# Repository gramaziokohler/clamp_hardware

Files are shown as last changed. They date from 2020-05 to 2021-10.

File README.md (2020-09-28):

# clamp_hardware

Mechanical design for remote controlled robotic actuators. This includes various clamps and grippers. 

This repo is part of the [Robotic Assembled Timber Structures with Integral Timber Joints](https://github.com/gramaziokohler/phd_spatial_timber_assembly) project. 

## Repo folder structure

Mechanical design files (Rhino 3D files, production drawings), ordered by clamp and gripper types:

- **/clamps** - Robotic clamp design 
- **/grippers** - Robotic gripper design

Experiment setup (Rhino 3D files, photographs, writeup) including results and interpretation.

- **/experiments** - Physical tests constructed and performed to validate mechanical design.

## Design Goals

The mechanical design of the clamps is to be able to achieve the following functions: 

- Deliver high assembly force to assemble tight-fitting timber joints
- The clamps cannot relocate itself but rely on robotic manipulator (such as a robotic arm) for locomotion.
- The clamps can be temporarily attached to a timber beam and operate remotely.
- Different clamp designs accommodate different types of timber joints, some clamp design can accommodate a joint type with various angles.

## Clamp Design

### Clamp CL1

**Cross Lap Joint** Clamp for **Planar Orthogonal** joint angle. Timber section size 100mm x 100mm.

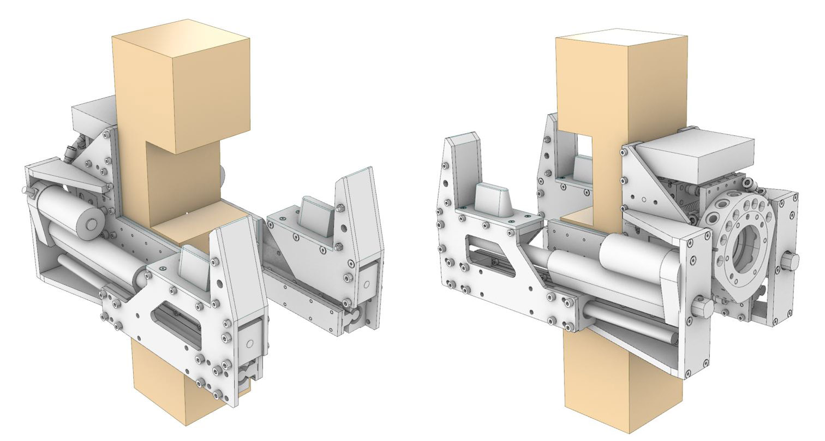
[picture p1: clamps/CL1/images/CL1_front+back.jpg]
CL1_front+back


This is the first clamp prototype with off-the-shelf actuator and two jaw design. This proof-of-concept device successfully performed a single joint assembly task. 

This prototype exposed the limitation of off-the-self linear actuators which were designed to deliver push force, not pull force. 

- Maximum assembly force ~400kgf.
- Robotic quick changer integrated but not tested
- No remote control capability
- Linear actuator gear box housing failed during stress test

### Clamp CL2

**Cross Lap Joint** Clamp for **Planar Orthogonal** joint angle. (similar to CL1)

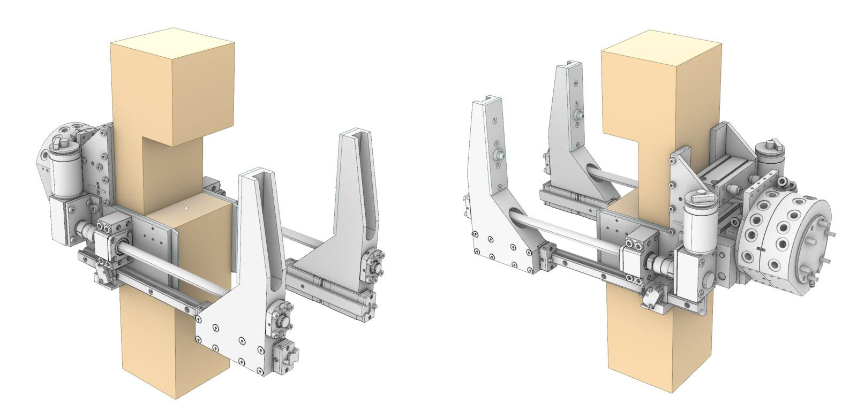
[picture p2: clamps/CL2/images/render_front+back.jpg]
render_front+back


This clamp is an improved version from **CL1** with similar design goals and capability. The main modification is the development of a **single piece jaw design** by combining linear guide mount and ball nut mount into a single piece of milled aluminum. This jaw design is the result of two important experiments mentioned in the next section.

Notable improvements:

- Reliable power transfer mechanism
- Reliable DC Encoder motor
- Lighter weight than CL1
- Modular jaw construction

This clamp was designed and materials were prepared but were never assembled for testing. The materials was then used to create TL1 for the Tokyo project. Since the tests performed with TL1 was successful and the 

### Clamp TL1 (tokyo)

**Tee Lap Joint** Clamp for **Planar Variable** joint angle. Timber section size 120mm x 120mm.

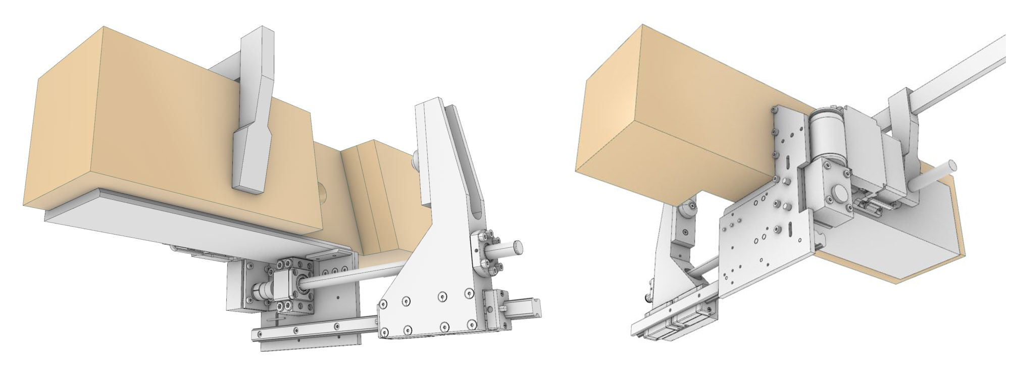
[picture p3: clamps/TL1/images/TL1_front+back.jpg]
TL1_front+back


This clamp is designed specifically for the GKR Tokyo Pavilion project with revised linear actuator design using ball screw and encoder DC motor. It has one clamp jaw that presses on the middle of the lap joint.

Two units of this clamp was created and two experiments were performed on assembling timber beams in during the Tokyo project. 

- No robotic quick changer integration
- Remote control and battery operation tested
- Two way synchronization not tested

Notable mechanical features:

- Single piece jaw design (combining linear guide mount and ball nut mount)
- Highly reliable worm-geared DC motor with dual channel encoder
- Small number of custom-piece

### Clamp CL3

**Cross Lap Joint** Clamp for **Planar Variable** joint angle.

 render_front+back

CL3_Front+Back

This clamp is a continuation of the single piece jaw design originated from CL2 and tested in TL1. 

The clamp is used in the construction of Fred's Pavilion where the robotic quick changer is not integrated.

Battery Compartment Size: 82(L) x 37(W) x 46(H)

## Validation Experiments

[**Ball Screw Actuation Experiment**](./experiments/190910_Screw_And_Motor_Test) - After the failure of the prototype clamp CL1 with integrated linear actuator, the decision is to construct the linear actuation from ball screw and motor from parts. This test validate the selection of ball screw and motor by testing the pull force developed.

[**Linear Guide and Clamp Jaw Experiment**](./experiments/191111_Linear_Guide_Jaw_Test) - Learning from the experience of the prototype clamp CL1, the circular linear guide combination with linear actuator was insufficient to prevent small rotational movements. This experiment was devised to assess replacement with a rolling-ball linear guide and the corresponding clamp jaw design. The conclusion of this experiment leads to the development of the single-piece jaw design for clamp TL1 and CL2

[**Joint Press**](./experiments/200100_Joint_Press) - CNC controlled joint pressing machine to measure the tightness of a lap joint. (Device designed but not constructed)

[**Lap Joint Tightness vs Rotational Stiffness Experiment**](./experiments/191113_Joint_Tightness_Stiffness_Study) - Experiment to study the rotational stiffness of lap joints in relation to the tightness of the joint. Tightness is measured by the amount of assembly force used to assemble the joint. (Experiment planned but not performed due to budget constraint)

[**Hollow Screw Tightening Torque Measurement**](./experiments/200903_LucaScrewMeasurement)  - Experiment to study the tightening torque of Luca's hollow screw in wood. This allows gearbox and motor sizing for Clamp SL1 

Credits
-------------

This repository was created by Pok Yin Victor Leung <leung@arch.ethz.ch> [@yck011522 ](https://github.com/yck011522) at [@gramaziokohler](https://github.com/gramaziokohler)

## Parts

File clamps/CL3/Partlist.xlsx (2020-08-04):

Block Name | Total | 4 Clamps Total | Source
Arduino Nano (LoRes) | 1 | 4
CL3 Electronics Pack | 1 | 4
ControllerPCB | 1 | 4
Fixed End Support BK10 | 1 | 4
Flat Head Socket Screw M4x12 | 3 | 12 | PHY-Shop
Flat Head Socket Screw M4x16 | 4 | 16 | PHY-Shop
Flat Head Socket Screw M4x20 | 9 | 36 | PHY-Shop
Flat Head Socket Screw M4x30 | 2 | 8 | PHY-Shop | x
Flat Head Socket Screw M4x8 | 4 | 16 | PHY-Shop | x
Flat Head Socket Screw M5x10 | 2 | 8 | PHY-Shop | x
Flat Head Socket Screw M8x20 | 4 | 16 | RFL
GripperPin | 6 | 24
Hex Nut M5 | 6 | 24 | void
HGL15CA | 2 | 8
KJL06-01S | 2 | 8
KQ2V06-M5A1 | 2 | 8
KQ2V06-M5A1.step | 2 | 8
KQ2V06-M5A1.step_BUTTON_06O | 2 | 8
KQ2V06-M5A1.step_KQ2(V-VS-VD-VT-VF-Z-ZD-ZT-ZF)_V06-M5 | 2 | 8
KQ2V06-M5A1.step_STUD_VZC_M5 | 2 | 8
LED 5mm | 2 | 8
M10 SFU Nut | 1 | 4
Motor Driver XY160D | 1 | 4
MXQ16-40P.step_AxialPipingUnit_16 | 1 | 4
MXQ16-40P.step_MXQ3149Tube_16-40 | 1 | 4
MXQ16-40P.step_MXQTables_16-40 | 1 | 4
Omron V-155-1C25_MircoSwitch | 1 | 4
Phoenix Plug Female ScrewTerm 2Pos | 8 | 32
Phoenix Plug Female ScrewTerm 3Pos | 1 | 4
Phoenix Plug Male PCB 2Pos | 8 | 32
Phoenix Plug Male PCB 3Pos | 1 | 4
Rigid Coupler SRJ-25C-8 | 1 | 4
SFU 1204 Nut | 1 | 4
Socket Head Cap Screw M3x16 | 2 | 8 | PHY-Shop |  | x
Socket Head Cap Screw M3x20 | 2 | 8 | PHY-Shop |  | x
Socket Head Cap Screw M3x8 | 8 | 32 | PHY-Shop
Socket Head Cap Screw M4x12 | 9 | 36 | PHY-Shop |  | x
Socket Head Cap Screw M4x16 | 15 | 60 | PHY-Shop | Polish | x
Socket Head Cap Screw M4x50 | 1 | 4 | PHY-Shop |  | x
Socket Head Cap Screw M4x8 | 4 | 16 | PHY-Shop
Socket Head Cap Screw M5x20 | 1 | 4 | PHY-Shop |  | x
Socket Head Cap Screw M5x30 | 3 | 12 | PHY-Shop |  | x
Socket Head Cap Screw M6x16 | 1 | 4 | RFL
Socket Head Cap Screw M6x20 | 1 | 4 | RFL
Socket Head Cap Screw M6x35 | 6 | 24 | PHY-Shop |  | x
Wireless CC1101 | 1 | 4
Dowel Pin 8x16 or 8x15 | 1 | 4 | PHY-Shop |  | x
Dowel Pin 6x10 or 6x12 | 1 | 4 | PHY-Shop |  | x
Dowel Pin 5x10 5x12 | 2 | 8 | PHY-Shop |  | x

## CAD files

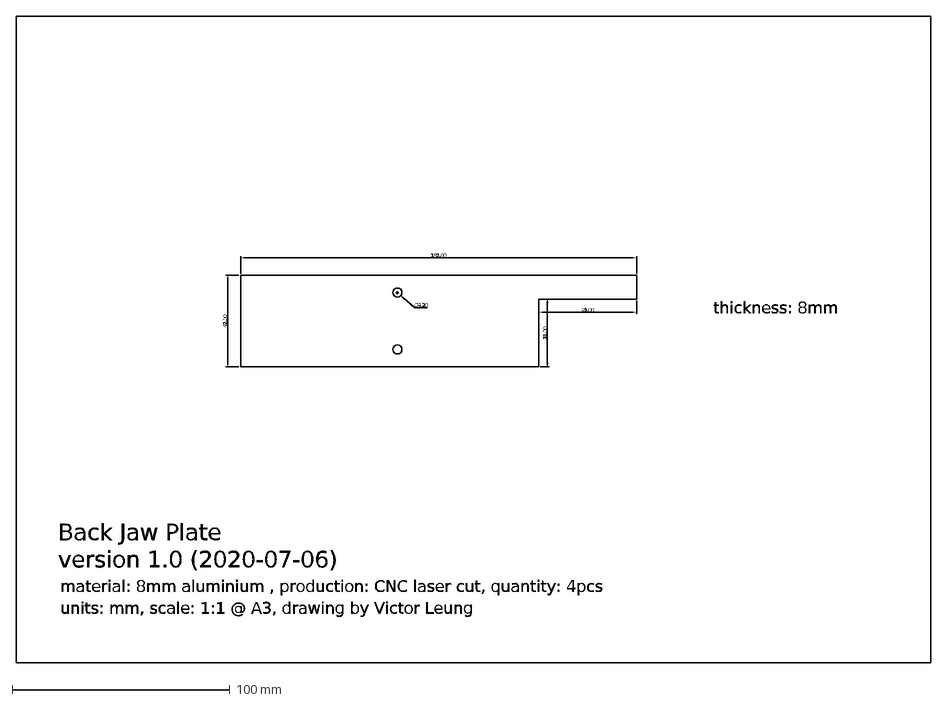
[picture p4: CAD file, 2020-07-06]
clamps/CL3/drawings/back_jaw_plate_v1.0.dxf
Ø4.20
31.00
45.00
42.00
182.00
material: 8mm aluminium , production: CNC laser cut, quantity: 4pcs
thickness: 8mm
Back Jaw Plate version 1.0 (2020-07-06)
units: mm, scale: 1:1 @ A3, drawing by Victor Leung

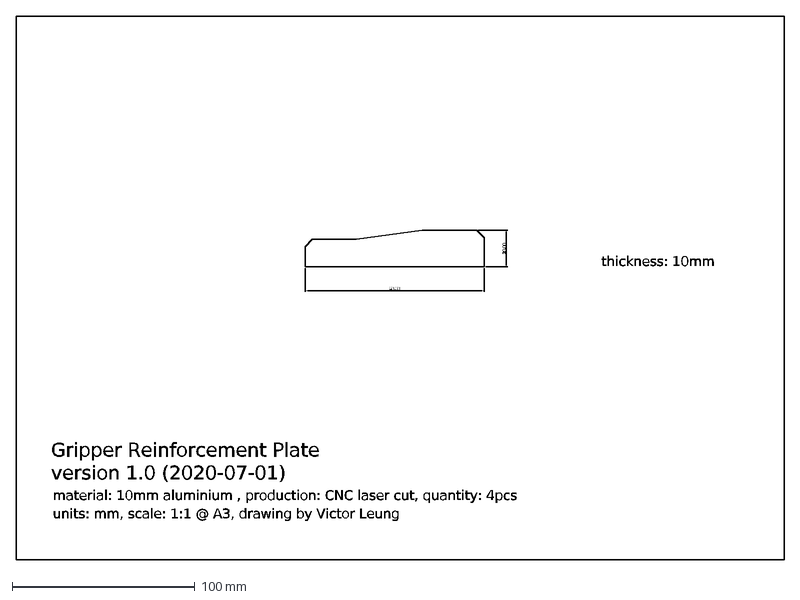
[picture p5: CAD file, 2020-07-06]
clamps/CL3/drawings/gripper_reinforcement_plate_v1.0.dxf
20.00
98.00
Gripper Reinforcement Plate version 1.0 (2020-07-01)
material: 10mm aluminium , production: CNC laser cut, quantity: 4pcs
thickness: 10mm
units: mm, scale: 1:1 @ A3, drawing by Victor Leung

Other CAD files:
drill_guide/3dp/drill_check_mainslide.3mf
clamps/SL1/3dp/MainBody.stl
camera/3dp/100mm_cover.stl
clamps/CL3/3dp/limit_switch_block.stl
clamps/SL1/3dp/SwitchHolder.3mf
drill_guide/3dp/32mm Drill guide.3mf
experiments/200109_Pickup_Station_Test/PickupStationAlignmentPeg3mm.stl
experiments/200115_Gripper_Nipple_Test/Jaw_NippleCone01.stl
experiments/200711_Robotic_PickPlace_Actions/3dp/clamp_jaw_pad_tester.stl
experiments/211023_ChamferPlaneAttachment/attachment_v1.3mf
grippers/PG/3dp/PGStorageBlock_i3mk2s.3mf
toolchanger/3dp/ts_dummy_base.stl
toolchanger/toolchanger_guide/3dp/robot_side_guide.stl
camera/3dp/100mm_stand.stl
clamps/CL3/3dp/jaw_pad.3mf
clamps/SL1/3dp/DriverCover.3mf
camera/3dp/70mm_cover.stl
camera/3dp/70mm_stand.stl
camera/3dp/MountPlate.stl
camera/3dp/MountStand.stl
camera/3dp/MountStand2.stl
camera/Aruco_marker_board.3dm
clamps/CL1/CL1_design.3dm
clamps/CL2/CL2_design.3dm
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

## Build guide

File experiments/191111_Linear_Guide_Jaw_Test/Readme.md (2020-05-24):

# Clamp Jaw Test

This set of test investigate the limiting criteria in jaw design. Especially in answering the following questions:

- Will the Linear Guide be overloaded?

- Can the linear guide be mounted cantilevered?

What is the minimum throat size of the L Shaped Jaw

What is the most flexible component in the system.

Motor 555 Gear 55:1

Test Date 2019-11-27 (till 28)

## Test 1 - Voltage vs Pull Force Test

The first test is to establish the relationship between voltage and pull force.

Similar to previous screw pull force test.

### Parameters

Different limiting current is used in each set, voltage is varied.

### Result

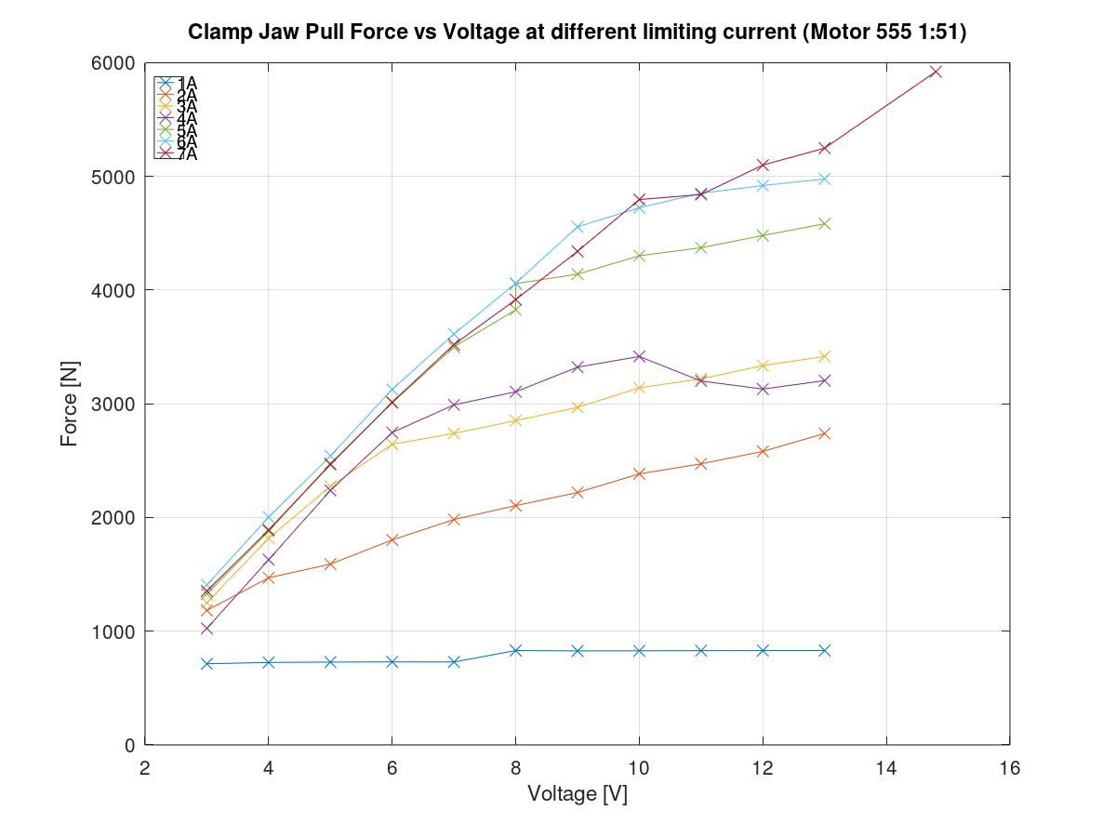
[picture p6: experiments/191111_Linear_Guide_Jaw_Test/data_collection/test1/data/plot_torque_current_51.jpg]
plot_torque_current_51


Note that the last data point of the 7A series at 14.4V is actually using the LiPo Battery as power source.

Two slopes can be seen here in the graph:

**The first steep slope** is when the motor is limited by the supplied voltage (Power supply in Constant voltage mode). Increase in supplied voltage is followed by an increase in supplied current. Therefore the motor can pull harder.

**The second slope** occurs at at point where the motor is limited by the set current limit. (Power supply is in constant current mode) The terminal current is limited and the motor will not be able to pull harder. However, there is still an increase in the pull force with voltage probably due to the higher voltage, hence faster motor speed and momentum, before terminal position. This momentum contribute to the final pulling force. 

## Test 2 - Spacing between linear bearing

Investigate different linear bearing spacing.

Look for difference in pull force, visual observation of L shape jaw deflection?

### Parameters

Test will involve 5 possible positions: 74mm, 87mm, 100mm, 126mm, 152mm.

Each position will use three different current: 3A, 4A, 5A

Voltage set beyond the current limit point of the 5A situation: 9V

### Result

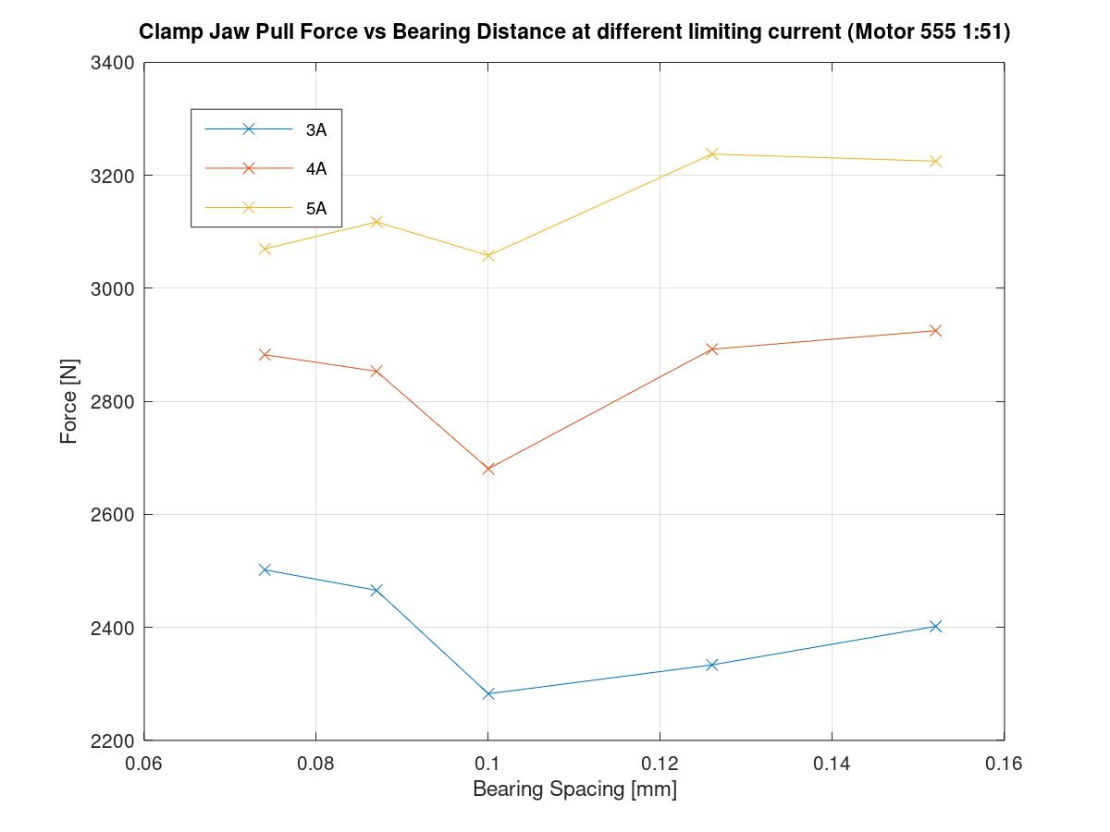
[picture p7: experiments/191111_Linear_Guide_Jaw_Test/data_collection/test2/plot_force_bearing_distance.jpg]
plot_force_bearing_distance


Only one set of data is collected. Due to time consumption in relocating the bearing.

However, it is still conclusive that the bearing distance do not have much effect on the pull force. 

We can conclude that the bearing distance in the clamp design, is only limited by overloading.

The bearing distance can be further reduced to 66mm in final design.

## Test 3 - Two bolts mounting Linear Rail

Investigate when the linear rail is more cantilevered. When only the last two bolts are used to hold it.

### Parameters

Fixed Voltage at 14V, current increase from 3A upwards.

The steel U profile is modified. The previous hole for the screw to go through is too small, the screw scratches on the steel.

| Current | Pull Force (Max Value) |
| --- | --- |
| 3 | 3154 |
| 4 | 4459 |
| 5 | 5167 |
| 6 | 5138 |
| 7 | 6086 |

Only one set of pull test is performed. As the jaw successfully puled about 6kN, the test was not continued to avoid damaging components.

### Result

- The structure deformed but remain intact after repeated pull test. 
- The linear rail do not deform at all, the steel is very strong.
- The Linear bearings even though at only 74mm spacing, do not seem to be overloaded.
- The L Shape Jawdeform the most. Perhaps if the L piece have a triangulated chamfer, the jaw structure could be more stiff. However, the plat interfere with the screw bearing.

## Test 4 - Worm drive gearbox

Investigate if the 555 motor paired with the GW4058 1:54 or 1:72 gearbox will have similar pull strength. 

This gearbox is a major space-saver.

### Parameters

Different limiting current is used in each set, voltage is varied.

### Result

Worm gearbox cannot be back driven and the stored tension do not reverse the motor after power is removed.

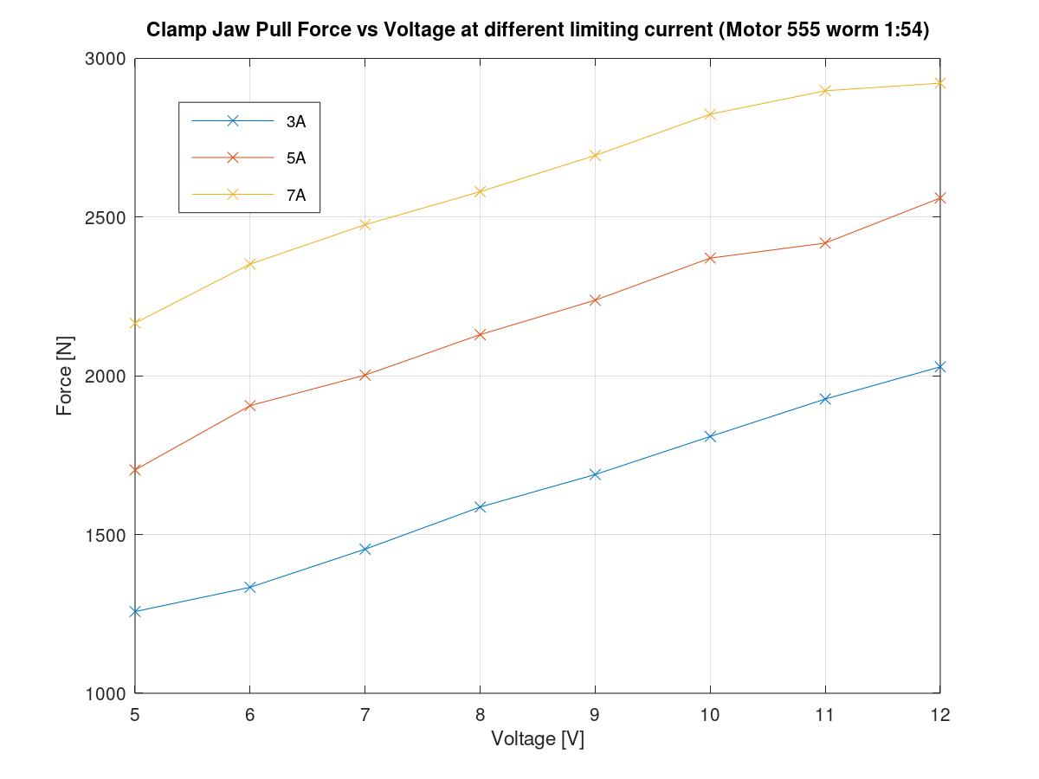
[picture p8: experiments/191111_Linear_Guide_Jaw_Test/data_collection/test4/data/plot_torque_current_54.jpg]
plot_torque_current_54


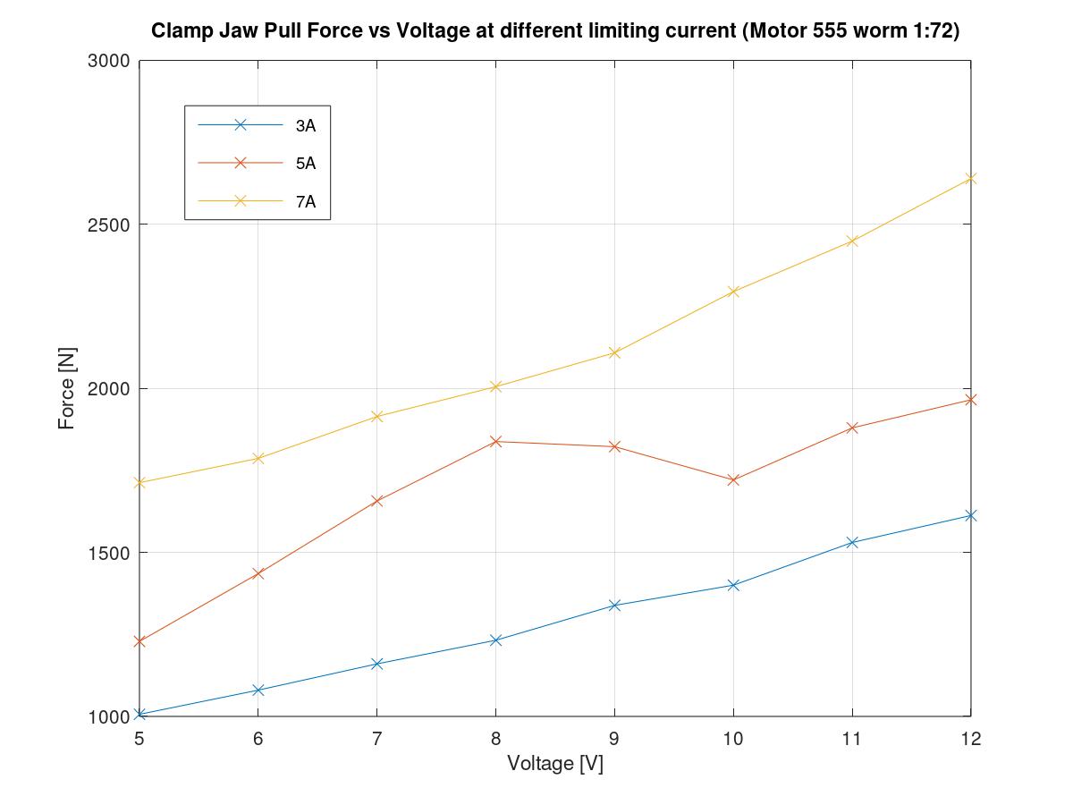
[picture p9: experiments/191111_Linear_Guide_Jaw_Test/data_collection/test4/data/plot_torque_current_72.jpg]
plot_torque_current_54


It is surprising to see that the **1:54 gearbox perform better** than the 1:72 gearbox in similar voltage current setting. This is probably due to a lower efficiency of the 1:72 gearbox. 

The results seems to be much more linear than the planetary gearbox, without the distinctive 2 slopes.

Comparing with Test 1 which has a 1:51 planetary gearbox, the pull force is much lower. @ 7A 12V this gearbox can pull **2900N**, compared to **5100N** in Test 1.

### Li-Po Battery test

A follow up test using the 4 Cell Lipo Battery (14.8V 1300mAh 45-90C)

| Gear Box | 1:54  | 1:72  |
| --- | ----- | ----- |
| Pull Force with LiPo | 4900N | 4450N |

The pull force can reach **4900N** at stall. This implies it has the gearbox has the potential to deliver the high torque without damage. The 1:54 gearbox is performing better in this case too.

# General observations

The motor mount using the factory supplied L shape brackets is not ideal, the shaft coupler blocks the access to the M3 Screws. 

The U shaped steel for mounting load cell to the test base profile is deforming under load.

The aluminum L shaped jaw is permanently deformed by about 0.4 degrees. This should be improved in the final design.

The flat face plate in the jaw moved due the slippage. the oversized hole in the aluminums plate  allowed the M4 screws to move.  This should be restrained in the future.

# Next Step

A velocity controlled motor movement, using the feedback control and Arduino and motor driver board can be tested in this setup. It is important to see if the ultimate pulling force will be reduced under such controlled movement speed.

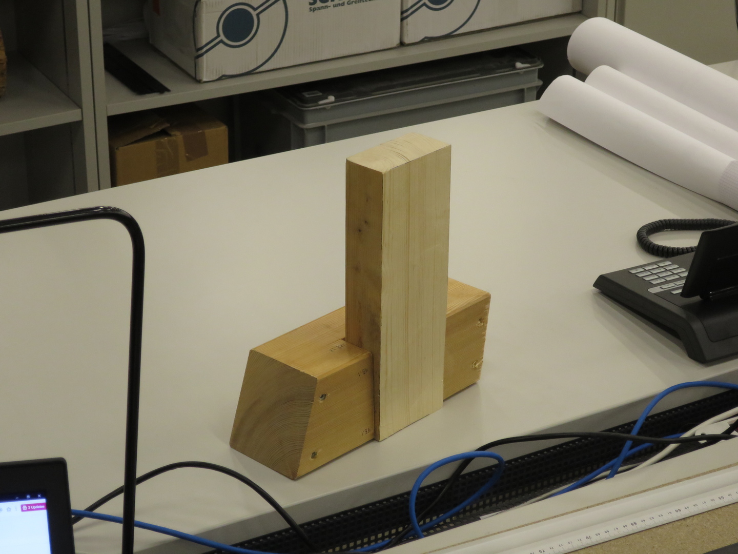
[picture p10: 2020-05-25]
experiments/191113_Joint_Tightness_Stiffness_Study/Photo/191209_Manual_Tightness_Test_02_VL_thumb.jpg

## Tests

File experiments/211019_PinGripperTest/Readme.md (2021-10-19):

Pin Gripper Hole Drilling Test

The purpose of this test is to check if the pin gripper system work with the drilled holes. In particular we would like to validate the drill hole spacing and angles.

##  Setup: Drilling

The drilling setup uses a 3D printed grill guide, the angle and separation of the holes can be seen in the drawing. The central 18mm hole is also drilled even though no left-in screw is used in the test.

 manual_drill_guide

IMG_20211019_134328_Edited



## Setup: Pin Gripper Pins

A partially assembled clamp is used. One bronze and one steel pin (has a nut for more leverage) was used. They are manually rotated by hand holding onto the shaft, no pliers were used. 



## Result

The clamping mechanism reached reasonable tightness at around 25mm extension (measured parallel to the main screw), it is also possible to force both screws to 30 mm extension by force, although I think this is not necessary in practice. 

Repeated use of the same hole shows some wear, probably by local crushing. On subsequent runs, both screws can be easily extended to 30mm extension, clamping force is still reasonable.

## Conclusion

I believe it is perhaps best to drill the diagonal holes manually in the production run. The accuracy I have achieved in this manual drill guide is rather high due to the precisely made drill guide and it is being clamped accurately to the wood.

I'm not sure if the CNC fabricator is willing to fine tune the machine for us to achieve similar results.

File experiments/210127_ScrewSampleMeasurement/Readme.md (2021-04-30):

# Notes about Screw sample ordered from China

The order is placed on TaoBao. The technical drawings given to the manufacturer are  [Left_In_Screw_11.pdf](Setup\Left_In_Screw_11.pdf)  and  [Left_In_Screw_20.pdf](Setup\Left_In_Screw_20.pdf) 

In general the screw we got back looks good.  Threads are sharp and debris cutting slots are sharp.

## Mistakes 

Screw head hole pattern is not correct. Hole sizes are too small. 

Screw head holes should not be drilled through were drilled through.



Screw threads external diameter are smaller (17.57mm) than the drawing (18.00mm). This wasn't explicitly communicated to the manufacturer. 



## Next Order

Things to consider in next order. 

- Screw head needs to be corrected
- Screw threads external diameter needs to be larger. The test with torque proves that Luca's screw with a 18mm external diameter will struggle with the 15mm hole but okay with a 16mm hole. 
- I believe we should use a 16 mm hole to reduce entry torque. I suggest the tolerance of the external diameter to be between 17.80 to 18.00mm 
- Screw shoulder and thread length see the design study below

## Design Study

The following anticlastic roof surface provides rough estimation of the screw length and how many to order. 



There are two types of joints requiring screws, planar lap joint (requiring shorter screw)  and non-planar lap joints (requiring shorter screw). Image below show both types of joints.



Based on this study, length suggestions (mm):

| | Joint Thickness | Screw Shoulder + Head Length | Screw Thread Length | Total Length |
| --- | --- | --- | --- | --- |
| Planar Joint | 40 - 60 | 40 | 40 | 80 |
| Non-Planar Joint | 60 - 70 | 60 | 50 | 110 |

Alternatively, both screw can have the same shoulder length (and different thread length to keep overall length as recommended) to simplify manufacturing.

Number of screws on the structure:

| | Primary Structure | Primary Bracing | Secondary Beams | Rafter | Total |
| --- | --- | --- | --- | --- | ----- |
| Planar Joint | 12 | 34 | | | 46 |
| Non-Planar Joint | | 4 | 16 | 88 | 108 |

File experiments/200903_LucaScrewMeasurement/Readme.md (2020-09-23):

# Hollow Screw Tightening Torque Measurement

The goal of this measurement is to find the necessary torque need to tighten the hollow screw designed by Luca Steiner. The result will be used for sizing motor and gearbox for driving the screw.

## Test Setup

### Screw

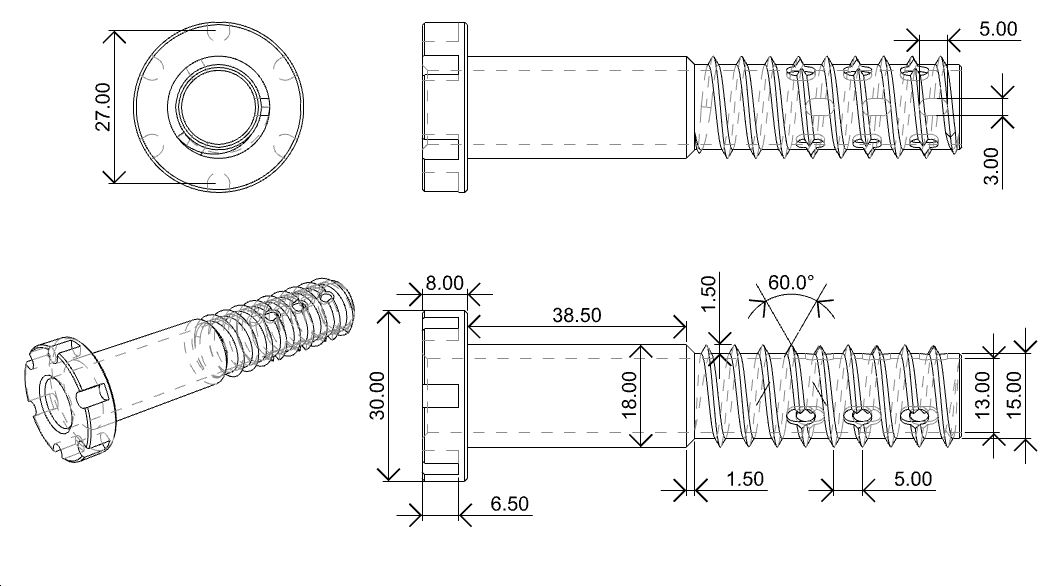
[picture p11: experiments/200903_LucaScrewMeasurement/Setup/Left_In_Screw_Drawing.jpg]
Left_In_Screw_Drawing


### Wood

A short section of 100x100mm spruce wood with 15mm holes drilled at the center line.

### Torque measuring Device

The torque measuring setup consist of a jig that allows the wood sample to rotate and press against a 300kg load cell. 

The load cell is placed 50mm offset from the rotation center.

We used a Bosch battery drill with a custom adapter to rotate the screw. 

## Results

30 holes samples were measured and the maximum torque required is 19.25Nm.

The general trend is a higher torque required when the screw in deeper.

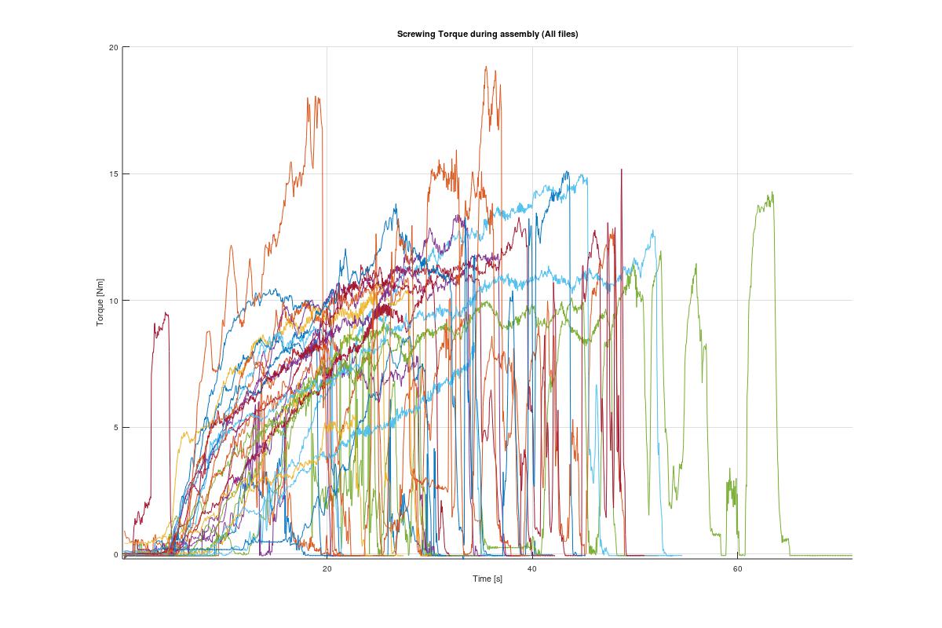
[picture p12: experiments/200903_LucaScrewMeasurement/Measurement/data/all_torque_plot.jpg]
all_torque_plot


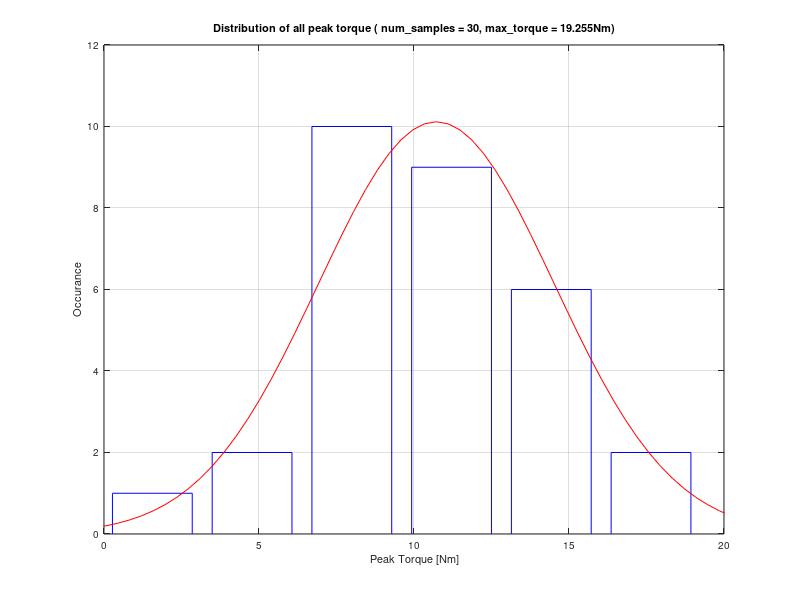
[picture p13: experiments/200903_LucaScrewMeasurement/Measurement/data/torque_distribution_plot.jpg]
torque_distribution_plot


In cases where the rotation is stopped and restart, we do not observe a a higher peak needed to restart the motion.

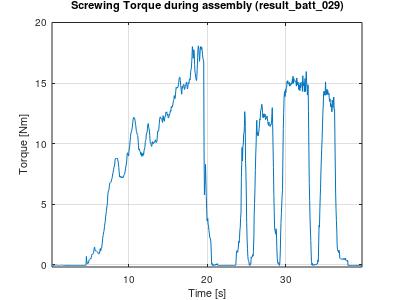
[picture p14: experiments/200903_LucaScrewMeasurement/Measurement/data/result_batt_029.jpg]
result_batt_029


## Next steps

Jamming might occur if the screw and the drilled hole is exactly the same diameter. Which in this experiment was 15mm. In production, 0.1 to 0.2mm diameter difference would prevent jamming.

If a shorter screw is used, the required torque could be lowered.

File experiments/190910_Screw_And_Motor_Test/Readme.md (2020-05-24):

# Ball Screw and Geared DC Motor Test

The goal of this test is to find if newly sourced ball screw and the DC motor can deliver forces that are higher than the previous integrated actuator (~200kg). 

The linear actuation drive train consist of the following parts:

- 36GP - 555 DC Motor with Hall Effect Encoder
- Hiwin Compatible Ball Screw 1204 300mm
- Hiwin Compatible Ball Nut 1204
- Hiwin Compatible Screw Support - BK10
- Shaft Coupler

Linear guide is not included and not tested in this experiment.

## Test Setup

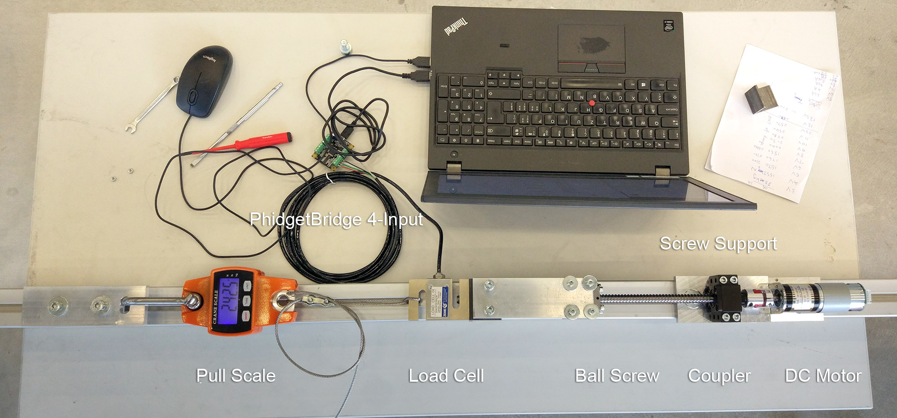
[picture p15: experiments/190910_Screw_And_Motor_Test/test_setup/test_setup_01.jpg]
test_setup


Test setup with both **loadcell** and **pull scale** (for loadcell calibration) attached to the test jig.

### Motor - 36GP-555

 https://item.taobao.com/item.htm?spm=a1z09.2.0.0.32392e8dqyPg5S&id=544216961663&_u=jl5jjmhf0dd 

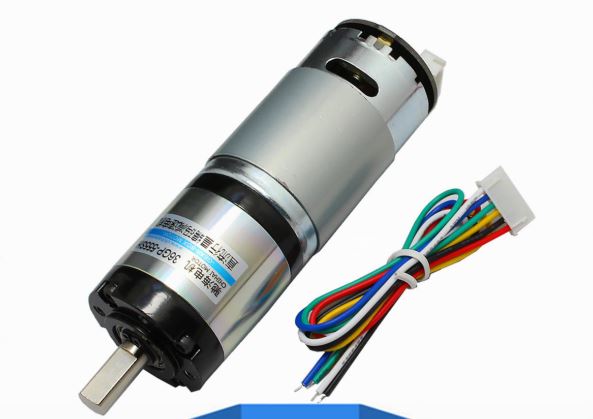
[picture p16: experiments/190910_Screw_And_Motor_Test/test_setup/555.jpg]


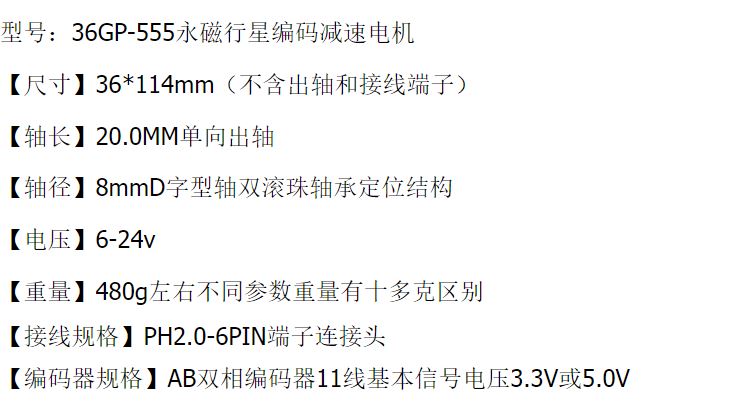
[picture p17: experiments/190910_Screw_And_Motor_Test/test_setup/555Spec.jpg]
555Spec


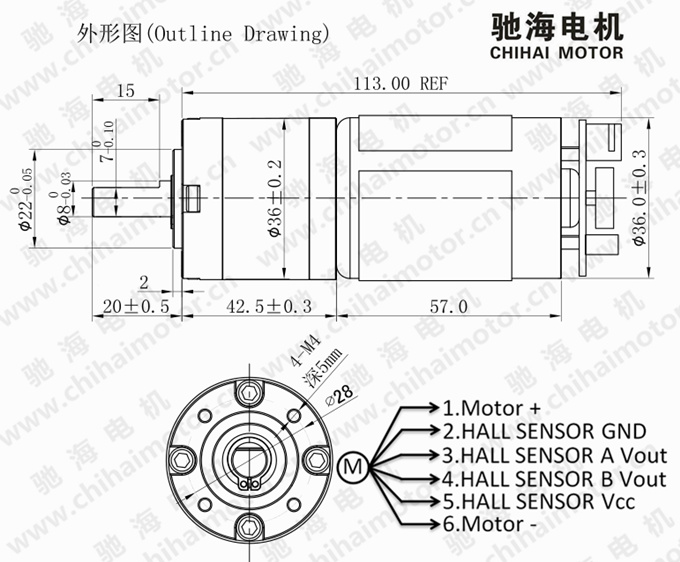
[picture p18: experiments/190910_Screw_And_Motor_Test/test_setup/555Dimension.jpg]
555Dimension


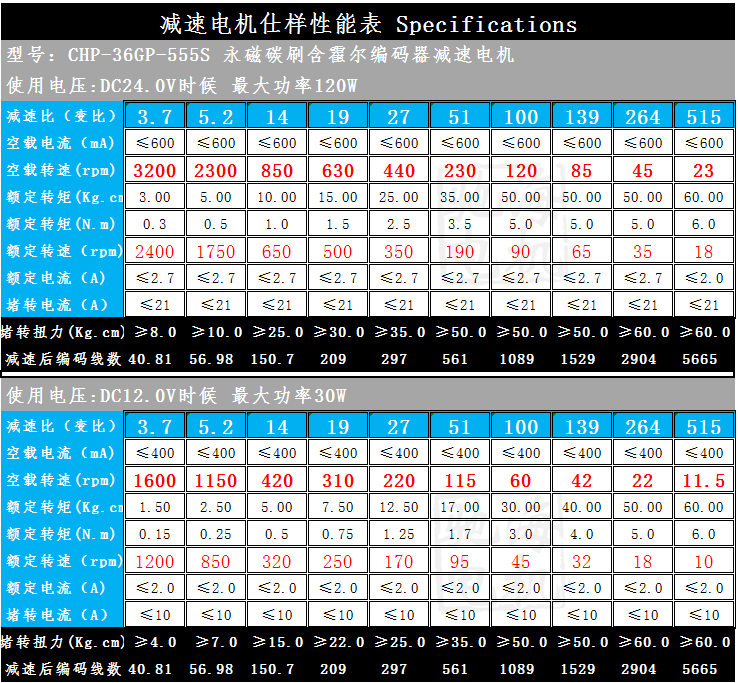
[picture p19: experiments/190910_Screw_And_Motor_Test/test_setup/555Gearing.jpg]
555Gearing


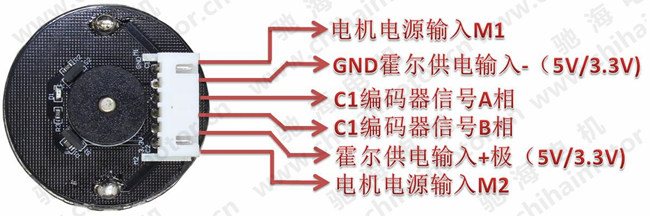
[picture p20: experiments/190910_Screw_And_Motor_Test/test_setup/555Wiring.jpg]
555Wiring


Two motors gearbox are tested:

According to specification:

| Gearbox Ratio | 12V No Load Speed | 12V Loaded Speed | Rated torque [Kg.cm] |
| --- | --- | --- | --- |
| 1:51 | 115 rpm | 95 rpm | 3.43 |
| 1:100 | 60 rpm | 45 rpm | 4.90 |

### Ball Screw 1204 

Ball screw ordered from TaoBao, model number is SFU1204

Similar product can be found in HiWin:   [RBS-R12-4B1-FSB-200-261-0.05](https://motioncontrolsystems.hiwin.com/item/ballscrews-main-configurator/ballscrews-main-configurator/rbs-r12-4b1-fsb-200-261-0-05) 

3D Model found on GrabCAD:  https://grabcad.com/library/sfu1204-500mm-with-bk10-bf10-set-1 

screw_components

ball_nut

### Support BK10

BK10 was used with another end being free end. 

3D model was found in HiWin: [BK10](https://motioncontrolsystems.hiwin.com/item/all-categories/support-units-bk-series/bk10?plpver=1001) 

Another similar model FK10 can be used too but not tested: [FK10](https://motioncontrolsystems.hiwin.com/item/all-categories/support-units-fk-series/fk10-a)

support_types

screw_support_spec

### Shaft Coupler SRJ-25C

shaft_coupler

### Nut Support DSG12H

nut_support

nut_support_spec

### Power Supply

Bench top power supply is used to provide a DC voltage for the test.

Note that this is different from a PWM controlled power supply. But this decision is made simply for reducing the unknown involved in these test. 

## Variables

The (large one) power supply is used and set at constant voltage mode with current limiting feature.

Different current limit is tested to simulate a different battery discharging capability: 2A to 7A

Different voltage is tested to simulate the effect of different battery voltage and PWM control: 2V- 14V

The motor is allowed to **run free until it is stalled**, power is then cut to avoid burning the motor. The screw typically rewinds itself due to stalled compressive force in the mechanical system. This is **repeated 5 times**. The **maximum pulling force recorded** from the load cell is logged as the maximum pulling force.

## Results

plot_torque_current_51

plot_torque_current_100

## Conclusion

### Maximum Pulling force vs Battery Voltage

The steeper initial diagonal slope represents a voltage limiting factor. Such as the case of a high discharge rate **LiPo battery**, operating at a certain voltage. The relationship is rather linear and consistent. 

This can be sued to deduce the **maximum pulling force** a specific **LiPo battery voltage** can deliver.

### Current Limiting

The less steep slope represent the current limiting situation. In the case where the current is limited, the maximum pulling force still improves as voltage increase. This is probably due to the higher speed that is built up during the free rotating phase of the test before the terminal force is reached, the momentum helped increase the force.

### Comparing two gearbox

The general trend of the two gear box are similar. But the graph is scaled to be higher.

The 1:100 gearbox have higher pull force (steeper initial slope) in the same testing voltage and current. It is very possible that if a high current is used in the test, the higher torque will damage some components.

It seems that the higher geared motor is more suitable to be used with a lower voltage battery where 

### Deliver 5kN force

Lets assume we would like to deliver 5kN of force for our application, which is should be enough for closing most joints. (This is yet to be confirmed with closure force test) . 

The 1:51 motor will require 9V and consumes 6A (assuming current is not limiting factor)

The 1:100 motor will require 4.5V and consuming 4A.

The 1:51 motor will spin **faster** and have more reserved **capacity for speed control**.

The 1:100 motor will be **slower** but have more chance to **overcome local stick-slip behavior**.

## Next Step

Repeat the test with a PWM controlled power supply.

Different PWM values are used and the maximum pulling force is observed.

(This future test will be performed with the L shaped jaw)

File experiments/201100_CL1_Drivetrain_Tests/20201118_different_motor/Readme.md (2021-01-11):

# CL1 Drivetrain Test with 15 and 16 mm holes

The goal of this test is to determine the suitability of the 775 motor in performing the screwing task in CL1 design.

Two 775 motor are run at 14.4V using 4-cell Li-Po battery, with different planetary gearbox. Motor diameter is 42mm, length is 66.5mm without gearbox or encoder. The encoder has unknown pulse per motor rotation, and planetary gearbox ration is unknown. However combined step/sec is determined experimentally. 

The CL1 prototype has a secondary 1:20 worm drive gearbox that is tested together.

| Gear Box | 1:13 (2 stage) | 1:49 (3 stage) |
| --- | --- | --- |
| Rated torque (Nm) | 2 | 3 |
| Rated RPM (min<sup>-1</sup>) | 150 | 60 |
| Rated current (A) | <=6 | <=3.5 |
| Steps per planetary gearbox revolution | 915 | 2960 |
| RPM of motor and planetary gearbox at 2000steps/s (rpm) | 131.1 | 40.5 |
| Steps per secondary (1:20) gearbox revolution. | 18300 | 59200 |
| Time for 1 secondary rev at 2000steps/s  (seconds) | 9.15 | 29.6 |
| RPM after 1:20 drive (min<sup>-1</sup>) | 6.55 | 2.02 |

The screw used in this test is the long screw made by Luca. The threaded part is 50mm long (10 rotation).

## Test Result

### 1:13 Gear - 2000steps/s - Dry Run (before changing plastic tube)

result_2020-11-18_15-07-15

### 1:13 Gear - 2000steps/s - No base plate

result_2020-11-18_15-11-30

### 1:13 Gear - 2000steps/s - No worm gear

result_2020-11-18_15-13-22

### 1:13 Gear - 2000steps/s - No load (Base Line)

result_2020-11-18_15-09-39

### 1:49 Gear - 2000steps/s - No base plate

result_2020-11-18_15-20-30

### 1:49 Gear - 2000steps/s - No load (Base Line)

result_2020-11-18_15-21-51

### 1:49 Gear - 3000steps/s - No load (Base Line)

result_2020-11-18_15-22-33

### 1:49 Gear - 2000steps/s - 15mm hole 

#### Start (#1) ~25%

result_2020-11-18_16-00-10

#### Start (#2) ~25%

result_2020-11-18_16-40-26

#### End (#1) ~65%

result_2020-11-18_16-09-03

#### End (#2) ~70%

result_2020-11-18_17-16-48

### 1:49 Gear - 2000steps/s - 16mm hole 

#### Start (#1) ~25%

result_2020-11-18_16-15-18

#### Start (#2) ~25%

result_2020-11-18_16-30-37

#### End (#1) ~60%

result_2020-11-18_16-22-28

#### End (#2) ~60%

result_2020-11-18_16-36-58

### 1:13 Gear - 2000steps/s - 16mm hole 

#### Start (#1) ~70%

result_2020-11-18_18-05-09

#### Start (#2) ~40%

result_2020-11-18_18-11-20

#### End (#1) ~80%

result_2020-11-18_18-08-38

#### End (#2) ~70%

result_2020-11-18_18-18-55

### 1:13 Gear - 2000steps/s - 15mm hole 

#### Start ~50%

result_2020-11-18_18-22-09

#### Stalled ~100%

result_2020-11-18_18-24-51

## Summary

| 2000 steps / second Result | 1:13 | 1:49 |
| --- | --- | --- |
| Max Power @ No worm gearbox | 20% | |
| Max Power @ No base plate | 20% | 25% |
| Max Power @ No load (Base line) | 30% | 25% (30% @ 3000s/s) |
| Max Power @ 16mm hole | 80% | 60% |
| Max Power @ 15mm hole | Stalled | 70% |

## Conclusion

The 1:13 Gearbox Motor cannot insert the screw to completion when the hole size is 15mm. When the hole is 16mm, it is possible but consumes 80% of power with observable brush sparks and heat-up.

The 1:49 can reliably screw in entire 50mm screw length in either 15mm or 16mm hole scenario. The maximum power draw is 70% in 15mm hole, leaving some reserve for safety margin.

In general it is a good idea to have a **hole size larger then the inner diameter** (15mm) of screw. This should accommodate tolerance in hole center alignment. 16mm is perhaps too much, 15.5 might be more suitable. 

The 16mm screw hole is still very strong in final pullout force. However **pull force** in initial engagement could be lower and reduce the pull-together force that helps assemble the joint. 

The **reaction rotation force** is very high. This may increase the pressure between the lap joint shoulder faces when being rubbed and thus increase friction.

We can potentially run the 1:49 motor at 3000 step/sec (Stage1 : 60.7 rpm / Stage 2: 3 rpm) for screwing operation, and even higher speed for no load movements.

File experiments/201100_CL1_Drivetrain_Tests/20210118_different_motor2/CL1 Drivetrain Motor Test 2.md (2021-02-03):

# CL1 Drive Train Motor Test 2

This experiment is a follow up of the previous motor test, to determine if newly sourced motors are better at delivering the required torque, and at what speed.

The test setup is largely the same with previous test "CL1 Drivetrain Test with 15 and 16 mm holes". However **only 16mm holes** will be used as it is observed to require less torque and perhaps less accuracy in hole alignment. **Higher speeds** will also be test because these motors are larger. Focus will be on the 2nd stage output speed of the system.

775 motor specification is varied highly from source to source, here I used the spec sheet from HengJie for a more direct comparison with their other motors. Turns out the Hengjie is not very careful assembling and shipping their products, I received wrong gearbox combination from what I intended to order. I ended up having to open the gearboxes to back-calculate the gear ratio by myself.

The multi-stage planetary gearbox have a fixed ring gear across all stages. All of them have 46 gears regardless of gearbox size. The gear ratio of each step can be determined by the number of teeth on Ring vs Sun: (Teeth-on-ring) / (Teeth-on-sun) + 1

Observed gear box gear teeth and ratios:

| Sun Gear | Planetary Gear (3 planets) | Ring Gear | Calculated Ratio (reduction) | |
| --- | --- | --- | --- | ---- |
| 8 | 19 | 46 | 6.75 | |
| 11 | 17 | 46 | 5.1818 | |
| 14 | 16 | 46 | 4.2857 | |
| 17 | 14 | 46 | 3.7058 | |

Motors I end up receiving:

| Motor | HJX42RH71i / 775 | HJX45RM35i | HJX45RM51i | HJX50RNA27i | ~~HJX50RNA~~ |
| --- | --- | --- | --- | --- | --- |
| Test ID | Motor #1 | Motor #2 | Motor #3 | Motor #4 | |
| Motor Size | **⌀42**x66.5 | **⌀45**x66 | **⌀45**x66 | **⌀50**x88 | **⌀50**x88 |
| Gearbox Ratio (reduction) | 71.16 | 34.97 | 50.89 | 22.21 | 51 ? |
| Gearbox combinations | (1+46/17) *<br />(1+46/11) *<br />(1+46/17) | (1+46/8) *<br />(1+46/11) | (1+46/17) *<br />(1+46/17) *<br />(1+46/17) | (1+46/14) *<br />(1+46/11) | |
| Gearbox Stages | 3 | 2 | 3 | 2 | 3 |
| Gearbox Length (mm) | 49.5 | 39.8 | 49.5 | 39.8 | 49.5 |
| Stall Torque (Nm) | 6.43 | 4.8 | 7.47 | 9.53 | 15.7 |
| Rated Torque (Nm) | **1.43** | **1.18** | **1.66** | **2.12** | **3.5** |
| Rated RPM (min<sup>-1</sup>) | 78.4 | 114 | 78.4 | 118.5 | 62.7 |
| Voltage (V) | 12 | 12 | 12 | 12 | 12 |
| Rated current (A) | 2.0 | 2.45 | 2.45 | 4.5 | 4.5 |
| Stall current (A) | 10 | 13.2 | 13.2 | 15.8 | 15.8 |
| Motor Power (W) | 20 | 27 | 27 | 42 | 42 |
| Theoretical Output (W) | 11.7 | 14.0 | 13.6 | 26.3 | 22.9 |
| Rated RPM after 1:20 drive (min<sup>-1</sup>) | **3.9** | **5.7** | **3.9** | **5.9** | **3.135** |
| Weight (g) | 734 | 717 | 813 | 1077 | |
| Price (CNY / CHF) | 225  (30.87) | 260 (35.67) | 265 (36.35) | 355 (48.70) | ~~365 (50.07)~~ |

Timber sample with 16mm hole.

New test regime with 16mm hole:

| Speed | No Load (One turn) | Load (16mm hole) (45mm travel / 9 turns) | Notes | |
| --- | --- | --- | --- | ---- |
| Test to confirm step to output ratio | Case #1 | | | |
| Test at fixed **Step** speed (3000 steps/s) | Case #2, 1 Sample  | Case #12, 2 Sample (3 if inconclusive) | | |
| Test at fixed **Stage 2 Output** Speed (3rpm) | Case #3, 1 Sample  | Case #13, 2 Sample (3 if inconclusive) | approx. 7 min / 100mm | |
| Test at fixed **Stage 2 Output** Speed (4rpm) | Case #4, 1 Sample  | Case #14, 2 Sample (3 if inconclusive) | approx. 5 min / 100mm | |
| Test at fixed **Stage 2 Output** Speed (5rpm) | Case #5, 1 Sample  | Case #15, 2 Sample (3 if inconclusive) | approx. 4 min / 100mm | |
| Test at fixed **Stage 2 Output** Speed (6rpm) | Case #6, 1 Sample  | Case #16, 2 Sample (3 if inconclusive) | approx. 3.3 min / 100mm | |
| Test at fixed **Stage 2 Output** Speed (8rpm) | Case #7, 1 Sample  | Case #17, 2 Sample (3 if inconclusive) | approx. 2.5 min / 100mm | |

## Case 1 (Ratio Test)

| Motor | #1 HJX42RH71i / 775  | #2 HJX45RM35i | #3 HJX45RM51i | #4 HJX50RNA27i |
| --- | --- | --- | --- | --- |
| Gear ratio | 71.16 | 34.97 | 50.89 | 22.21 |
| Encoder Steps | 64 | 64 | 64 | 64 |
| Theoretical Steps | 91,084 | 44800 | 65139 | 28428 |
| Steps tested | 91,084 over | 44800 over 2 mark | 65139 over 2.5 marks | 28428 over 4 marks |
| | 90084 over 1 mark | 44000 looks ok | 64000 over 0.5 mark  | 28000 over 2 marks |
| | 89000 under 1/4 mark | 88000 less 1 mark | 63800 over 0.5 mark  | 27700 looks good |
| | 89200 looks good | 88400 over 1.5 mark | 127600 over 0.5 mark | 55400 over 1/3 mark |
| | | 88000 less 1 mark | 127400 less 0.5 mark | 55300 less 1 mark (WTF) |
| | | 88150 over 1/4 mark | 127500 over 0.5 mark | 55380 less 0.5mark |
| | | 88100 over 1 marks (WTF) | | 55390 |
| Accepted | **89200** | **44000** | **63750** | **27700** |

## Case 2 to 7 (No Load)

Gear Ratios of each system. Formular for calculating **steps/s** based on : (target_rpm) x (steps/rev) / 60

| Motor | Case | HJX42RH71i / 775 | HJX45RM35i | HJX45RM51i | HJX50RNA27i |
| --- | ---- | --- | --- | --- | --- |
| Steps for 1 turn | | **89200** | **44000**  | **63750**  | **27700** |
| | 2 | 3000 ok | 3000 ok | 3000 ok | 3000 ok |
| Motor **steps/s** for **2nd stage 3rpm**  | 3 | 4460 ok | 2200 ok | 3187 ok | 1385 ok |
| Motor **steps/s** for **2nd stage 4rpm**  | 4 | 5946 ok | 2933 ok | 4250 ok | 1846 ok |
| Motor **steps/s** for **2nd stage 5rpm**  | 5 | 7433 ok | 3666 ok | 5312 ok | 2308 ok |
| Motor **steps/s** for **2nd stage 6rpm**  | 6 | 8920 fail | 4400 ok | 6375 ok | 2770 ok |
| Motor **steps/s** for **2nd stage 8rpm**  | 7 | ~~11893~~ | 5866 ok | 8500 fail  | 3693 ok |
| Motor **steps/s** for **2nd stage 10rpm** | 8 | | 7333 fail  | ~~10625~~  | 4616 ok |
| Motor **steps/s** for **2nd stage 12rpm** | | | | | 5540 ok |
| | | | | | 6200 ok |
| | | | | | 7000 fail |

## Case 13 to 18 (Screw into 16mm)

Case 1x is with Luca's screw

Case 2x is with new screw sample

| Motor | Case  | HJX42RH71i / 775 | HJX45RM35i | HJX45RM51i | HJX50RNA27i |
| --- | ----- | --- | --- | --- | --- |
| Steps for 10 turn | | **892000** | **404000** | **637500** | **277000/249300** |
| Motor **steps/s** for **2nd stage 3rpm**  | 13/23 | 4460 ok | 2200 ok | 3187 | 1385 |
| Motor **steps/s** for **2nd stage 4rpm**  | 14/24 | 5946 ok | 2933 ok | 4250 | 1846 |
| Motor **steps/s** for **2nd stage 5rpm**  | 15/25 | 7433 ok | 3666 ok | 5312 | 2308 ok |
| Motor **steps/s** for **2nd stage 6rpm**  | 16 | fail for sure | 4400 ok | 6375 | 2770 ok |
| Motor **steps/s** for **2nd stage 8rpm**  | 17 | | 5866 stall | | 3693 ok |
| Motor **steps/s** for **2nd stage 10rpm** | 18 | | | | 4616 ok |
| Motor **steps/s** for **2nd stage 12rpm** | 19 | | | | 5540 stalled |

## Case 30 Two Step Hole (10mm + 16mm hole)

Motor **#4** for 2nd stage 10rpm (4616 steps/s)

Sample 1 - 6 turns (149580)

Sample 2 - 10 turns (249300)

Sample 3 - 10 turns (249300)

Sample 4 - 1 turns (24930)

Sample 5 - 1 turns (24930)

Undo

Sample 6 - 1 turns (24930)

Sample 7 - 10 turns (249300)

Sample 8 - 10 turns (249300)

Sample 9 - 10 turns (249300)

Successful

# Summary

| Motor | HJX42RH71i / 775 | HJX45RM35i | HJX45RM51i | HJX50RNA27i |
| --- | --- | --- | --- | --- |
| Max RPM @ no Load | 5 | 8 | 6 | 13.5 |
| **Max RPM @ Screw 1, 16mm hole** | **5 (8 min for 200mm)** | **6 (6.6 min for 200mm)** | **5 (8 min for 200mm)** | **10 rpm (4 min for 200mm)** |
| | | | | |
| Weight (g) | 734 | 717 | 813 | 1077 |
| Price (CNY / CHF) | 225  (30.87) | 260 (35.67) | 265 (36.35) | 355 (48.70) |

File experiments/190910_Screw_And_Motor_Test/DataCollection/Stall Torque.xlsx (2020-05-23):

Current | Stall Voltage
 | Motor 1:51 | Motor 1:100
1 | 1.58 | 1.32
2 | 3.141 | 2.54
3 | 4.55 | 3.84
4 | 6 | 5
5 | 7.4
5.5 | 8.33
6 | 9.3
6.5 | 9.59
7 | 10.64

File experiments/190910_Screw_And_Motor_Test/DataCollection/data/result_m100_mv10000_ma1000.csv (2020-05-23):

Time | Time Since Begin | V/V Raw Data | Force
1574180383.3907247 | 0.2680642604827881 | 1.4092773e-05 | 15.415838259999994
1574180383.430712 | 0.30805158615112305 | 1.4109537e-05 | 15.47652394
1574180383.4707055 | 0.34804511070251465 | 1.4099292e-05 | 15.439437040000001
1574180383.5106928 | 0.3880324363708496 | 1.4088117e-05 | 15.398983539999996
1574180383.5586805 | 0.4360201358795166 | 1.4170073e-05 | 15.695664259999994
1574180383.5986712 | 0.476010799407959 | 1.4094636e-05 | 15.422582320000004
1574180383.638537 | 0.5158765316009521 | 1.4066696e-05 | 15.321439519999998
1574180383.67865 | 0.5559895038604736 | 1.4066696e-05 | 15.321439519999998
1574180383.7265074 | 0.6038470268249512 | 1.4084391e-05 | 15.385495419999998
1574180383.7665255 | 0.6438651084899902 | 1.4115125e-05 | 15.4967525
1574180383.8065038 | 0.6838433742523193 | 1.4144927e-05 | 15.604635739999999
1574180383.8464744 | 0.7238140106201172 | 1.4159828e-05 | 15.658577359999995
1574180383.8945937 | 0.7719333171844482 | 1.41114e-05 | 15.483268000000002
1574180383.9344592 | 0.8117988109588623 | 1.4094636e-05 | 15.422582320000004
1574180383.9745746 | 0.8519141674041748 | 1.4098361e-05 | 15.43606682
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

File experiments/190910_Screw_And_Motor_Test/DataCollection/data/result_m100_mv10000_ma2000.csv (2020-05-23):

Time | Time Since Begin | V/V Raw Data | Force
1574181722.6644788 | 0.2680041790008545 | 0.000143302605 | 483.1554301
1574181722.7045138 | 0.30803918838500977 | 0.000143078156 | 482.3429247199999
1574181722.7456746 | 0.3492000102996826 | 0.000142903998 | 481.71247275999997
1574181722.7867877 | 0.39031314849853516 | 0.000142718665 | 481.0415673
1574181722.834776 | 0.43830132484436035 | 0.00014261622 | 480.67071639999995
1574181722.8729134 | 0.4764387607574463 | 0.000142684206 | 480.91682572
1574181722.9129024 | 0.516427755355835 | 0.00014291238 | 481.7428156
1574181722.9528906 | 0.5564160346984863 | 0.00014303904 | 482.20132479999995
1574181723.0008776 | 0.604403018951416 | 0.000143319368 | 483.21611215999997
1574181723.0408707 | 0.6443960666656494 | 0.000143375248 | 483.41839775999995
1574181723.0807283 | 0.6842536926269531 | 0.000143328682 | 483.24982883999996
1574181723.1287243 | 0.7322497367858887 | 0.00014313776 | 482.5586912
1574181723.1687074 | 0.7722327709197998 | 0.000142925419 | 481.79001678
1574181723.2087097 | 0.8122351169586182 | 0.000142696314 | 480.96065668000006
1574181723.2487173 | 0.8522427082061768 | 0.00014265161 | 480.7988281999999
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

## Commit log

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2020-05-23 Moved here - Linear guide and jaw test
    [JawTest01.3dm, JawTest02.3dm, result_m51_mv10000_ma1000.csv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]
2020-05-25 Joint Press and tightness study added
    [191212_Sample_v2_VL.3dm, 191212_Sample_v2_VL.stp, Displacement_test_setup.3dm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]
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2020-06-09 CL1 CL2 TL1 design and images (Migrated from GKR server)
    [CL1_design.3dm, CL2_design.3dm, TL1_design.3dm]
2020-06-09 Pickup station and gripper nipple tests (Migrated from GKR server)
    [Gripper_Nipple.3dm, Jaw_NippleCone01.stl, Jaw_NippleCone02.stl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]
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2020-06-29 Minor 3D print parts tune - chamfer, printability, screw hole size.
    [CL3_design.3dm, electronics_base.stl, electronics_base_mirror.stl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]
2020-06-29 Fixed electronics base collision with spring pin
    [CL3_design.3dm, electronics_base.stl, electronics_base_mirror.stl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]
2020-07-06 Created Drawings for parts to be laser cut or machined.
    [clamp_back_plate_v1.0.dxf, clamp_front_plate_v1.0.dxf, gripper_reinforcement_plate_v1.0.dxf]
2020-07-06 Fixed incorrect position between Quickchanger and tool. Added back_jaw_plate drawing that is also laser cut.
    [CL3_design.3dm, back_jaw_plate_v1.0.dxf]
2020-07-09 PG1 Detailed Design and collision mesh model
    [PG1_design.3dm]
2020-07-09 CL3 Added some missing screws, Cleaned up blocks layers
    [CL3_design.3dm]
2020-07-09 Renamed PG1 to PG Series: such as PG500 PG1000
    [PG_design.3dm]
2020-07-09 Collision model updated to reflect the gripper's true closure which is 98.4 mm instead of 100mm. The limit of 100mm is implemented at the Gripper robotModel.
    [PG_design.3dm]
2020-07-09 Added tool changer and robot wrist collision model
    [toolchanger.3dm]
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2020-07-14 Galapagos based Best Fitting Frame over probed points
    [setup.3dm]
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2020-07-14 Probed a few more points with the dummy clamp at at better location
    [setup.3dm]
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2020-08-07 As constructed Clamp Adapter. CNC version not made
    [PG_design.3dm, PG_design_plate_CNC_version.3dm]
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2020-08-09 Tool Changer with IGPS Flange added (For planning with Gripper for Fred Pavilion)
    [toolchanger.3dm]
2020-08-10 CL3 Padding reduced, pin tapered, backjaw clearance added.
    [CL3_design.3dm]
2020-08-10 Further adjusted armpit padding, export padding for stl
    [CL3_design.3dm, limit_switch_block.stl, padding_armpit.stl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]
2020-08-11 Testing different max power setting and force output.
    [result_v2000_p20.csv, result_v2000_p30.csv, result_v2000_p40.csv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]
2020-08-11 Tested and tested and found a working limit switch block
    [CL3_design.3dm, limit_switch_block.stl]
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2020-09-23 CL3 Motor Cover that is easer to install
    [motor_cover.stl]
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2020-12-01 Refactored the first test result in the proposal.
    [result_2020-11-03_17-10-58.csv, result_2020-11-03_17-11-53.csv, result_2020-11-04_16-43-48.csv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]
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2020-12-03 CL1 Clamps Models with new bearing suggestion modelled.
    [SL1_Prototype.3dm]
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2021-01-11 SL1 with quick change hub and motor test plates
    [SL1_Prototype.3dm, qc_hub.stl]
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2021-01-13 motor plates and needle gripper mockup added to SL1 prototype
    [SL1_Prototype.3dm]
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2021-01-13 fixed error in pad where holes are missing
    [PG_design.3dm, StorageBlockBar1.stl]
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2021-01-21 Left in screw Head drawing for DIY drilling
    [Left_In_Screw.3dm]
2021-01-26 PG Gripper storage block combined in one piece
    [PG_design.3dm, StorageBlockCombined1.3mf, StorageBlockCombined1.stl]
2021-01-27 HJX50 Motor modeled, other tested motor plates removed.
    [SL1_Prototype.3dm]
2021-02-03 Screw Sample Measurement and Drivetrain 4 motors test
    [Screw1_Hole15_000.csv, Screw1_Hole15_001.csv, Screw1_Hole16_000.csv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]
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2021-02-08 Different options for the SL1 pin gripper actuation
    [SL1_Prototype.3dm]
2021-02-08 Step file of the tapered joint for the fabricator to test
    [191212_Sample_v2_VL.stp]
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2021-02-15 Storage Pad for PG and CL3 ready for 3dprint
    [PGStorageBlock.stl, PGStorageBlock_i3mk2s.3mf, PGStorageBlock_mini.3mf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]
2021-02-15 screw hole with bigger soulder for 25mm washer
    [PG_design.3dm]
2021-02-15 robot side with adapter plate found by Mike
    [robotside.3dm]
2021-02-16 Robot Side updated with found adapter. CL3M updated with corrected QC orientation
    [CL3_design.3dm, robotside.3dm]
2021-02-24 Cable mount updated with two more ziptie holes
    [robot_side_cable_mount.3mf, robot_side_cable_mount.stl, robot_side_cable_mount1.stl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]
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2021-02-26 Collision Mesh Made slightly smaller
    [robotside.3dm]
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2021-03-18 RPi Camera mount on toolchanger and Network setup
    [cam_holder_robot_side.stl, cam_holder_tool_side.stl, robotside.3dm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]
2021-04-02 Modified gripper gearbox plastic part with more space between guide
    [PinGripperGearbox.3mf, PinGripperGearbox.stl, SL1_Prototype.3dm]
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2021-05-05 Major Revision of SL1 adapter plates / electronics and minor revision of gearbox
    [DriverCase.stl, ESP32-CAM-Box.stl, ESP32-CAM-Lid.stl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]
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2021-05-08 Long list of update after reviewing with Marco - Pull screw designed by Marco - Pin gripper now use small motor - Pin gripper now attach via M5 - Magnets added - Pins added to hub - Freewheel hub ext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
    [BumperCableSide.stl, ControllerCase.stl, ControllerCover.stl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]
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2021-05-13 Updated Electronics case screw holes, zip tie holes, LED hole, Battery Plug location. Main shaft and keyway update
    [ControllerSplitCase.stl, SL1_Design.3dm, ScrewHoleTest.stl]
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2021-11-22 ESP Camera mount Inside CL3 Clamp Fix #4
    [CL3_design.3dm, cam_cover.3mf, cam_cover.stl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]
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2021-12-01 Driver Cover - added slot for main motor cables to enter. Front Bumper - added zip tie position for guiding pin gripper cables Encoder Cover - cover for main motor encoder
    [BumperGripperWireGuide.stl, DriverCover.stl, EncoderCover.3mf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]
2021-12-01 Bumper Adjusted for both Regular and Extended Version. Electronics Case (extended) adjusted for cable guide and thickened a thin wall Driver cover gap regularized with opposite side
    [BumperCableSide_Extended.stl, BumperCableSide_Regular.stl, BumperGripperSide_Extended.stl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]
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2021-12-02 Fixed bumper missing hole
    [BumperCableSide_Regular.stl, SL1_Design.3dm]
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2021-12-02 Screwdriver storage extended to 180mm wide Split into two print parts Fix #14
    [SL1_Design.3dm, ScrewdriverStorage.3mf, Storage.stl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]
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2022-01-17 Added GH file for marker CAD location and online calibration over ROS. Also include the correction calculation
    [robotside.3dm]
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2022-01-18 Grippers CM updated. - CM bigger on top of Toolchanger - CM bigger around gripper finger - Main bar thicker to cover pneumatic plumbing
    [PG1000.3dm, PG1500.3dm, PG500.3dm]
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2022-01-21 Pin changed to -ve X direction of base frame to match with already machined wood.
    [PG1000.3dm, PG1500.3dm, PG500.3dm]
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2022-02-09 Fixed Design Error preventing the inner slides to move
    [drill_check.3dm, drill_check_10mm.stl, drill_check_16mm.stl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]
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2022-02-09 fixed collision
    [drill_check_crossslide.3mf, drill_check_mainslide.3mf]
2022-02-10 Made cross slide looser
    [drill_check.3dm, drill_check_base.3mf, drill_check_crossslide.3mf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]
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2022-03-03 slightly tighter holes by changing xy offset from -0.12 to -0.08
    [SL1 Drill Guide - Slide.3mf]
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2022-05-18 Storage Collision Mesh
    [CL3_design.3dm]
2022-05-18 Updated CL3 storage pad collision mesh, storage linear move path.
    [CL3_design.3dm]
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2022-05-30 Added 5mm Jaw Pad and improved homing block stiffness
    [CL3_design.3dm, jaw_pad.3mf, jaw_pad.stl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]
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
